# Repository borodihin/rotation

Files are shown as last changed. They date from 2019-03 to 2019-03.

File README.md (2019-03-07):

# Rotation
This monitor rotation stand is inspired by Istructables <a href="https://www.instructables.com/id/Motorized-Sit-or-Stand-Landscape-or-Portrait-Monit/">project</a> and based on <a href="https://www.arduino.cc/">Arduino</a>, <a href="https://www.autohotkey.com/">Autohotkey</a> and Noël Danjou <a href="http://noeld.com/programs.asp?cat=misc#Display">Display</a> programm.

Monitor stand is produced from 12 mm plywood:

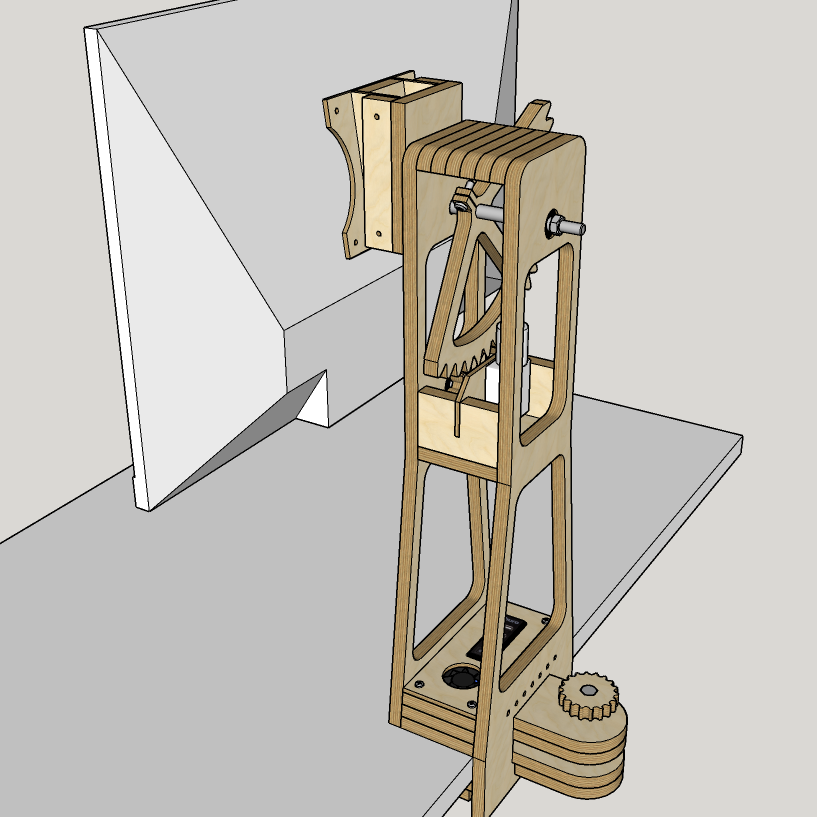
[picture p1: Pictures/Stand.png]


The display on this stand is rotated by <a href="https://www.aliexpress.com/item/DC-12V-30RPM-High-torque-Turbo-Encoder-Motor-Worm-Geared-Motor-Reducer-Motor-GM4632-370/32891279814.html">GM4632-370</a> DC 12V Geared-Motor, which drive 1:5 plywood gear reductor with 10- and 50-teeth gears as you can see on the picture below (I use only 144&deg; sector of 50-teeth gear). By the way, you can visit Matthias Wandel <a href="http://www.woodgears.ca/">site</a> where you can find many interesting videos and power tool to draw such gears.

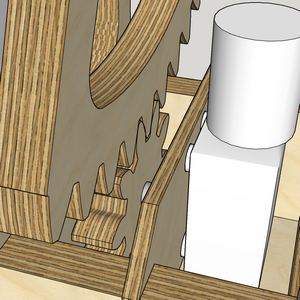
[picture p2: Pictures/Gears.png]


Used motor has a Hall encoder, so I can count turns to place display correctly in wide- and tall-position. The motor pinout is on scheme placed below:

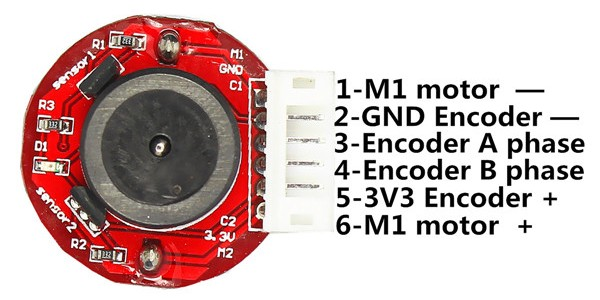
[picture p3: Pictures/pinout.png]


The motor is powered by L298N H-bridge driven by Arduino Nano as you can see on scheme below:

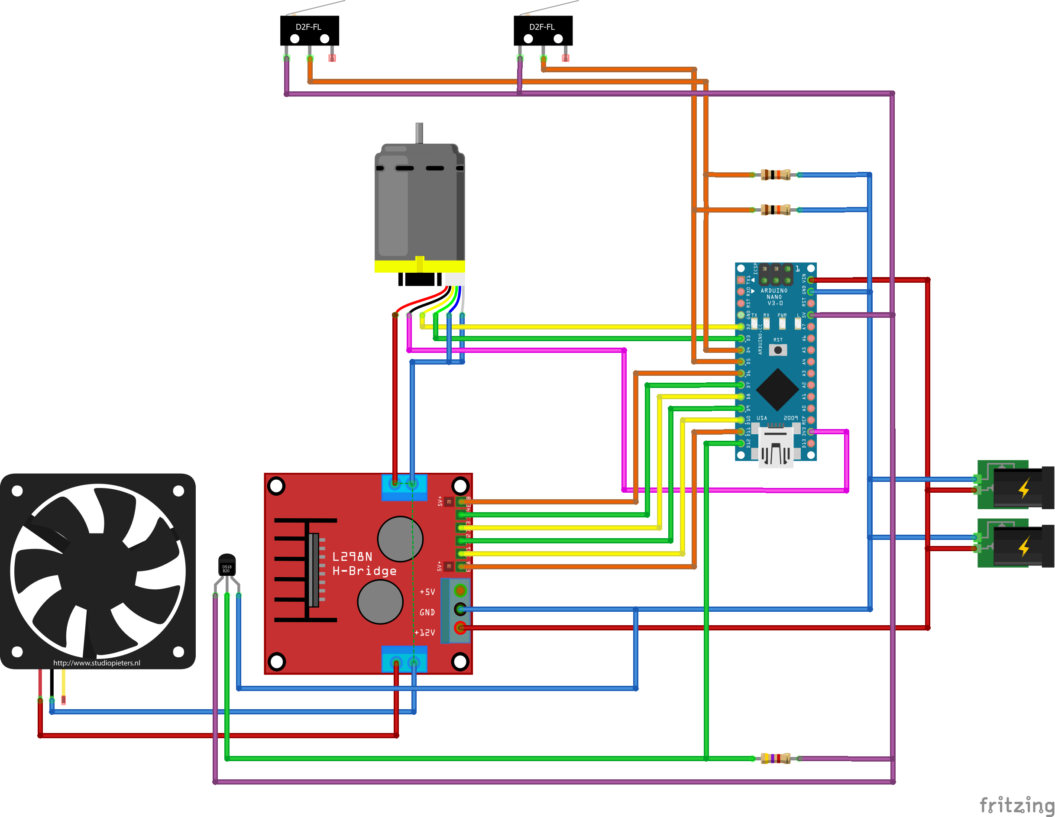
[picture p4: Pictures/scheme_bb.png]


There are two power jacks on this scheme because I have another DC 12V monitor placed near the stand and powered from this stand by the small cable.

All electronics placed in the small box formed on the stand base. For computer communication, the Arduino serial port is used. So there is a small 4-ports USB-hub in this project. Three ports are on its top and one is on the small side, placed under the top cover it is invisible:

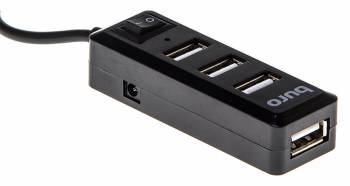
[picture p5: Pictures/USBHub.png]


So I desolder USB connectors from USB-hub and Arduino and use small wires to connect PCBs directly. In result, I have fully functional  USB-ports and full-time connected Arduino. By the way, there is an option to power this hub from the same DC 12V adapter using LM2596 step down <a href="https://www.aliexpress.com/item/Free-Shipping-1pcs-LM2596-LM2596S-DC-DC-4-5-40V-adjustable-step-down-power-Supply-module/32715399306.html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">converter</a> like this:

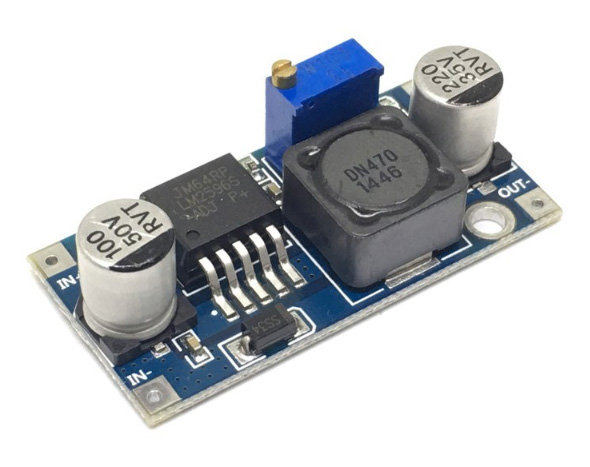
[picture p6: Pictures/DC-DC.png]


Electronics active cooling provided by small DC 12V fan powered from the second channel of L298N. Temperature is controlled by DS18B20 OneWire sensor.

There ate two endstop switchers placed on the top of the stand that used to stop motor to prevent mechanics damages. These pressed by the main big 50-tooth gear in its end positions.

When power is on first of all the display is rotated to its end position witch defined by the endstop switch pressed (power may be turned off directly on monitor rotating process and the display position is not clearly known) and then placed on the right wide-position. After that, I can turn the display to wide- or tall-position with binding Autohotkey keys (Win-F6 in the code) and sending command to Arduino using serial port:<br><code>RunWait, %ComSpec% /c echo o > COM3</code>,<br>where COM3 is my Arduino serial port. Same time I use Display program to change virtually display orientation and other connected displays positions, for examle:<br><code>RunWait, %ComSpec% /c "display.exe /device 1 /rotate 270 && display.exe /device 2 /position 1080 1472"</code>.

May be I will write some comprehensive code to synchronize Arduino and Autohotkey physical and virtual orientation, but now I can do in manually by pressing Alt-Win-F6 to place display virtual orientation to wide-position.

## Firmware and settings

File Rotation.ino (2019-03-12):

#include <Encoder.h>
#include <OneWire.h>
#include <DallasTemperature.h>

Encoder motorEnc(2,3);
OneWire oneWire(12);
DallasTemperature sensors(&oneWire);
float temp;

int fanPinOne = 8;
int fanPinTwo = 7;
int fanPinPWM = 6;

int monitorMotorPinOne = 9;
int monitorMotorPinTwo = 10;
int monitorMotorPinPWM = 11;

int endstopWidePosition = 300; // the value need to be experimentally defined
/*  
 *  We have two plywood gears with 10 and 50 teeth (1:5 reduction ratio).
 *  We need to rotate monitor wich attached to 50-tooth gear on 90 degrees,
 *  so it means that we need to rotate small gear on 450 degrees or 1.25 turn.
 *  Gearmotor has 11 impulses per motor shaft turn and 1:200 reduction ratio.
 *  So we have 2200 impulses per gear-end shaft turn and 2750 impulses at all.
 *  Something about 30 impulses per degree. Long monitor size is about 530 mm.
 *  530 * tan (1/30 deg) = 0.3 mm or 1.5 mm per 5 impulses (or half from center)
 *  Let use 5 impulses as rotation quantity.
 */
int wideTallPosition = 10500;

int CWendStopPin = 4; // CW rotation endstop button pin
int CCWendStopPin = 5; // CCW rotation endstop button pin

int CWendStopState; // CW rotation endstop state
int CCWendStopState; // CCW rotation endstop state
int incomingByte; // a variable to read incoming serial data into

int direction = 1; // rotation direction flag: 1 means CW; -1  means CCW

int oldPosition = -999; // encoder lowest position
int newPosition; // encoder current position

void setup() {
  Serial.begin(9600); // Serial port initialisation
  sensors.begin(); // One-wire initialisation
  
  pinMode(fanPinOne, OUTPUT);
  pinMode(fanPinTwo, OUTPUT);
  pinMode(fanPinPWM, OUTPUT);
  
  pinMode(monitorMotorPinOne, OUTPUT);
  pinMode(monitorMotorPinTwo, OUTPUT);
  pinMode(monitorMotorPinPWM, OUTPUT);

  pinMode(CWendStopPin, INPUT);
  pinMode(CCWendStopPin, INPUT);
  
  rotate(direction, 15000, 255); /* 5000 is a big number because we need to
  rotate until CW rotation endstop turns 1 to define starting position */

  direction = direction * (-1);
  rotate(direction, endstopWidePosition, 255);
}

void loop() {
  if (Serial.available() > 0) {
    // read the oldest byte in the serial buffer:
    incomingByte = Serial.read();
    if (incomingByte == 'o') {
      Serial.print("o is OK!");
      Serial.println();
      rotate(direction, wideTallPosition, 255);
      Serial.print("Rotation comlete! ");
      Serial.print(newPosition);
      Serial.println();
      direction = direction * (-1);
    }
  }

  sensors.requestTemperatures();  // Send the command to get temperature
  temp = sensors.getTempCByIndex(0); // Read temperature from the first sensor
  digitalWrite(fanPinOne, HIGH);
  digitalWrite(fanPinTwo, LOW);
  /* If temperature is 18 or low the fan is off. 
   * While temperature rising to 40 degrees PWM rising to 255
   */
  Serial.print("Temperature is: ");
  Serial.print(temp);
  Serial.println();

  //analogWrite(fanPinPWM, constrain(map(temp, 30, 40, 0, 255) ,0, 255));
}

void rotate(int dir, int steps, int PWM) {
  int startPosition;
  int stopPin;
  long timer;
  
  newPosition= motorEnc.read();
  startPosition = newPosition;
  if (dir == 1) {
    // CW rotation
    digitalWrite(monitorMotorPinOne, HIGH);
    digitalWrite(monitorMotorPinTwo, LOW);
    stopPin = CWendStopPin;
  } else {
    // CCW rotation
    digitalWrite(monitorMotorPinOne, LOW);
    digitalWrite(monitorMotorPinTwo, HIGH);
    stopPin = CCWendStopPin;
  }
  timer = millis();

  Serial.print(newPosition - startPosition);
  Serial.print(" ");
  Serial.print(dir * steps);

  Serial.println();

  while ((abs(newPosition - startPosition) < steps) && (digitalRead(stopPin) != HIGH)) {
    analogWrite(monitorMotorPinPWM, PWM);
    newPosition= motorEnc.read();
    if (newPosition != oldPosition) {
      oldPosition = newPosition;
    }
  Serial.print(newPosition);
  Serial.print(" ");
  Serial.print(startPosition);
  Serial.print(" ");
  Serial.print(dir);
  Serial.print(" ");
  Serial.print(steps);
  Serial.print(" ");
  Serial.println();

    
  }
  analogWrite(monitorMotorPinPWM, 0);
  Serial.print("Cutoff position = ");
  Serial.print(newPosition);
  Serial.print(" working time = ");
  Serial.print(millis() - timer);
  delay(1000);
  newPosition= motorEnc.read();
  if (newPosition != oldPosition) {
    oldPosition = newPosition;
  }
  Serial.print(", slowdown position = ");
  Serial.print(newPosition);
  Serial.println();
}
